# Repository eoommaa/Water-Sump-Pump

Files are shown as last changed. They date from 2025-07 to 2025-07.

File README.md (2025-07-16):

# Water Sump Pump Countdown Timer
A countdown timer for managing a water sump pump using a Raspberry Pi Pico programmed in MicroPython, designed for SLAC National Accelerator Laboratory during Summer 2024.
- **Features:** Automates sump pump intervals and relay activation with a 60-minute countdown timer, 3-button control (`START`/`STOP`/`RESET`), and thermal safety from 80°F fan activation to prevent overheating
  - Each button (`START`/`STOP`/`RESET`) is mapped to an LED and activates a specific state when the user presses on it
  - 60-minute countdown timer displayed in `MM:SS` format with the temperature on the LCD (`Countdown: 60:00` & `Temp: 80 F`)
  - **LCD Library from [`RPI-PICO-I2C-LCD`](https://github.com/T-622/RPI-PICO-I2C-LCD/tree/main) by [`T-622`](https://github.com/T-622):** [`lcd_api`](/src/lcd/lcd_api.py) & [`pico_i2c_lcd`](/src/lcd/pico_i2c_lcd.py)
- **Components:** [Full BOM](docs/BOM.md) with relay and sump pump specs

# Schematics[^1][^2]

## SLAC Water Sump Pump Countdown Timer Schematic


## RP2040 Water Sump Pump Countdown Timer Schematic


# Relay Behavior
Relay controls the 120 VAC outlet like a feedback loop.
- **[`SLAC Water Sump Pump Countdown Timer` Schematic](#slac-water-sump-pump-countdown-timer-schematic):** Pin 3 from `K1` relay has an input of 120 VAC L input (10 A) and Pin 4 is an input to the same 120 VAC output
- **`START`:** Relay NC[^3] &rarr; Sump pump activates
- **`STOP` & `RESET`:** Relay NO[^3] &rarr; Sump pump deactivates

# `START`/`STOP`/`RESET` Button Controls
## `START`/`STOP`/`RESET` Button State Diagram
```
               ┌──────────────────────────┐
               │                          ▼
┌────┐   ┌─────┴───┐   ┌────────┐   ┌─────────┐
│Idle├──►│START Btn├──►│STOP Btn├──►│RESET Btn│
└────┘   └─────────┘   └────┬───┘   └────┬────┘
              ▲             ▼            │
              └──────────────────────────┘
```

## `START` Button
- **Function:** Default state where the system starts 60-minute countdown timer
- **LED:** Blinking green

## `STOP` Button
- **Function:** Pauses the countdown timer
- **LED:** Solid red
- **LCD:** Displays messages repeatedly
  > Countdown stopped!
  
  > Press START or RESET
- [`countdown_stop = True`](https://github.com/eoommaa/Water-Sump-Pump/blob/d4ba52d33f075a21b61ff5ee6c35b372b952a699/src/water_sump_pump.py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) pauses the countdown timer

### `START` & [`RESET`](#reset-button) Button on `STOP`
- **`START`:** Countdown timer continues from the time it was paused on
  - **LED:** Red off and blinking green

## `RESET` Button
- **Function:** Emergency reset (Countdown timer restarts at `60:00` after the user presses `START` button)
- **LED & Buzzer** Blinking blue & buzzer beeps repeatedly
- **LCD:** Displays messages repeatedly
  > Countdown reset!
  
  > Press START to start over
- [`system_locked = True`](https://github.com/eoommaa/Water-Sump-Pump/blob/d4ba52d33f075a21b61ff5ee6c35b372b952a699/src/water_sump_pump.py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) allows the user one button to press on to restart the countdown timer
  - User can press on `STOP` or `RESET` button, but the program ignores the two button presses when in `RESET` mode

## Countdown Idle and Completion LCD Messages
- **Countdown Idle:** `Press START!`
- **Countdown Completion:** `Press START to start agn`

# Notes
- **[`SLAC Water Sump Pump Countdown Timer` Schematic](#slac-water-sump-pump-countdown-timer-schematic):** A `K1` relay is connected to the L298N motor driver, which is the component connected in the final hardware
- **[`RP2040 Water Sump Pump Countdown Timer` Schematic](#rp2040-water-sump-pump-countdown-timer-schematic):** A 5V DC motor is used since the relay acts like a switch along with an IC2 1602 LCD connected to the RP2040
  - Ex: Motor on when countdown timer is running and vice versa when it is off
- **Power Indicator:** Green LED stays on during both idle and after completion states to indicate that the Pi Pico is powered

# Credit
- **LCD Library:** Adapted from [`RPI-PICO-I2C-LCD`](https://github.com/T-622/RPI-PICO-I2C-LCD/tree/main) by [`T-622`](https://github.com/T-622)

[^1]: [`SLAC Water Sump Pump Countdown Timer` Schematic](https://github.com/eoommaa/Water-Sump-Pump/blob/main/kicad/schematics/SLAC%20Water%20Sump%20Pump.pdf) and [`.kicad_sch`](https://github.com/eoommaa/Water-Sump-Pump/blob/main/kicad/SLAC%20Water%20Sump%20Pump.kicad_sch)
[^2]: [`RP2040 Water Sump Pump Countdown Timer` Schematic](https://github.com/eoommaa/Water-Sump-Pump/blob/main/kicad/schematics/RP2040%20Water%20Sump%20Pump.pdf) and [`.kicad_sch`](https://github.com/eoommaa/Water-Sump-Pump/blob/main/kicad/RP2040%20Water%20Sump%20Pump.kicad_sch)
[^3]: Normally open (NO) & normally closed (NC)

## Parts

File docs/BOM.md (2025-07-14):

# Bill of Materials
*Note: Components used for prototyping*

| Hardware | Qty | Notes |
| :--: | :--: | :--: |
| Raspberry Pi Pico | 1 | RP2040 MCU |
| L298N Motor Driver | 1 | Fan & motor/relay control |
| 9V DC Battery | 1 | Power source for L298N motor driver |

| User Control | Qty | Notes |
| :--: | :--: | :--: |
| NO[^1] Buttons | 3 | `START`/`STOP`/`RESET` |

| User Feedback | Qty | Notes |
| :--: | :--: | :--: |
| LEDs | 3 | Green (`START`), Red (`STOP`), Blue (`RESET`) |
| I2C 1602 LCD | 1 | Displaying countdown time & temp |
| Piezoelectric Buzzer | 1 | Beeps on `RESET` button |

| System Feedback | Qty | Notes |
| :--: | :--: | :--: |
| 5V DC Fan | 1 | Thermal safety |
| 5V DC Motor | 1 | Relay testing |

| Passive Components | Qty | Notes |
| :--: | :--: | :--: |
| 330 &#8486; Resistors | 3 | LEDs current limiting |
| 100 &mu;F Capacitors | 3 | Button debouncing |

# Relay and Sump Pump Specs
*Note: Similar components connected in the final hardware*
| Components | Manufacturer Part Number | Datasheet | Notes |
| :--: | :--: | :--: | :--: |
| Relay | AZ9375-1A-24DEF | [AZ9375 SENSITIVE SUBMINIATURE RELAY](https://www.azettler.com/pdfs/az9375.pdf) | 12 VDC coil, 120 VAC (10 A) |
| Sump Pump | PF92342-PB | [PF92342 Thermoplastic Sump Pump](https://fergusonprod.a.bigcontent.io/v1/static/5097488_7397986_specification) | 2400 GPH at 0' lift |

[^1]: Normally open (NO)

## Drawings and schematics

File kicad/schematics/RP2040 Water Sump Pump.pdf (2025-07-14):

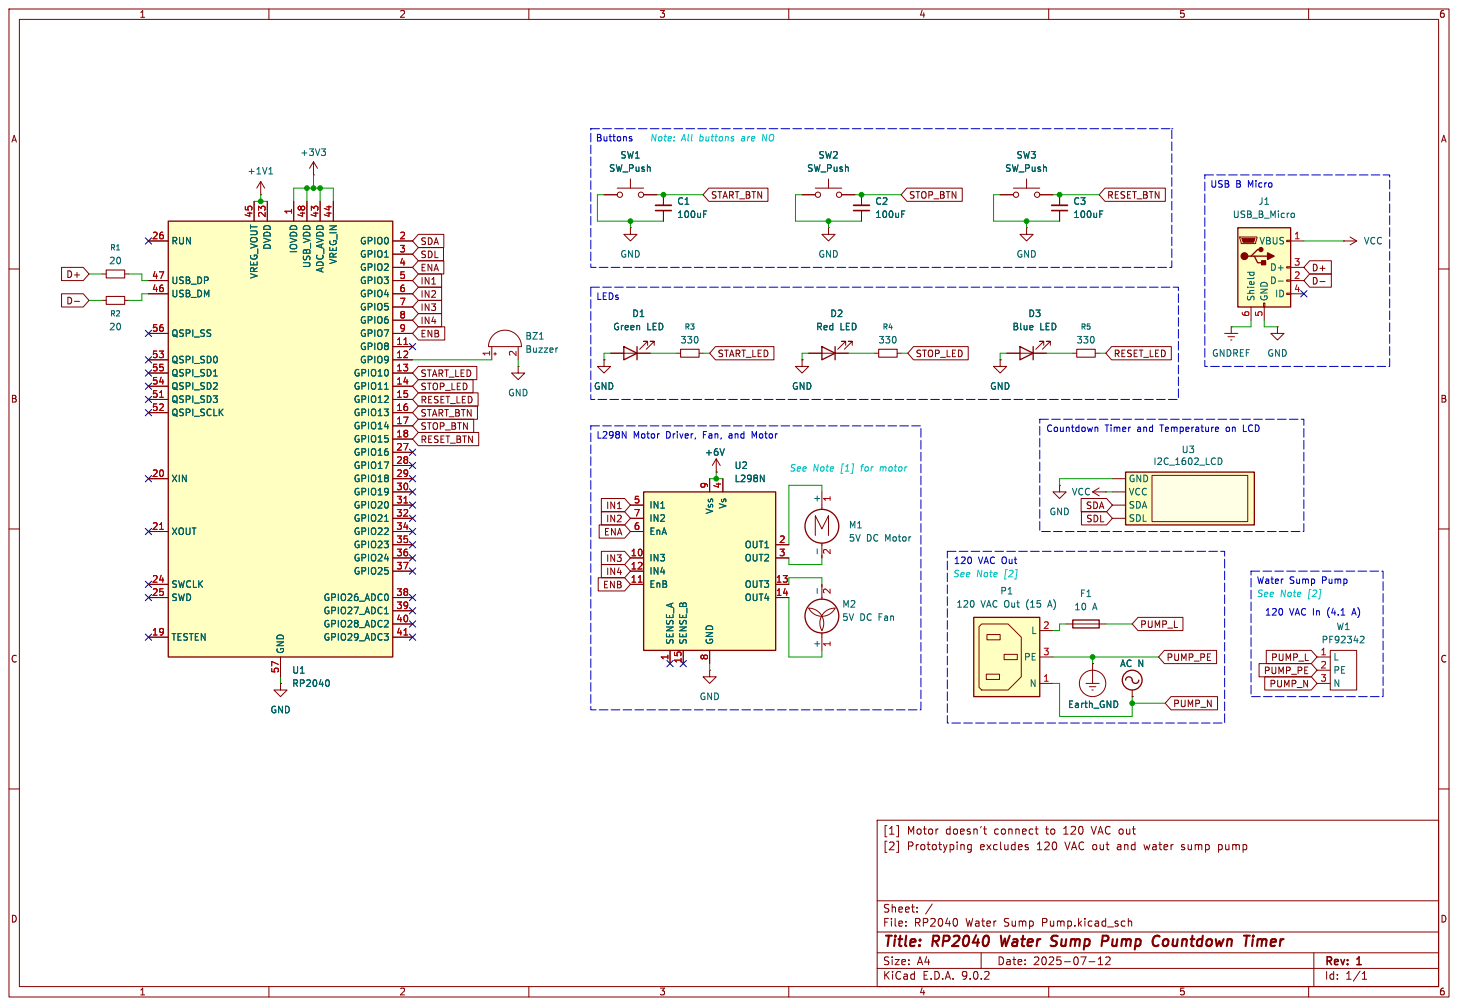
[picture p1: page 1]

L298N Motor Driver, Fan, and Motor C1

R4 330 D2 Red LED GND GND

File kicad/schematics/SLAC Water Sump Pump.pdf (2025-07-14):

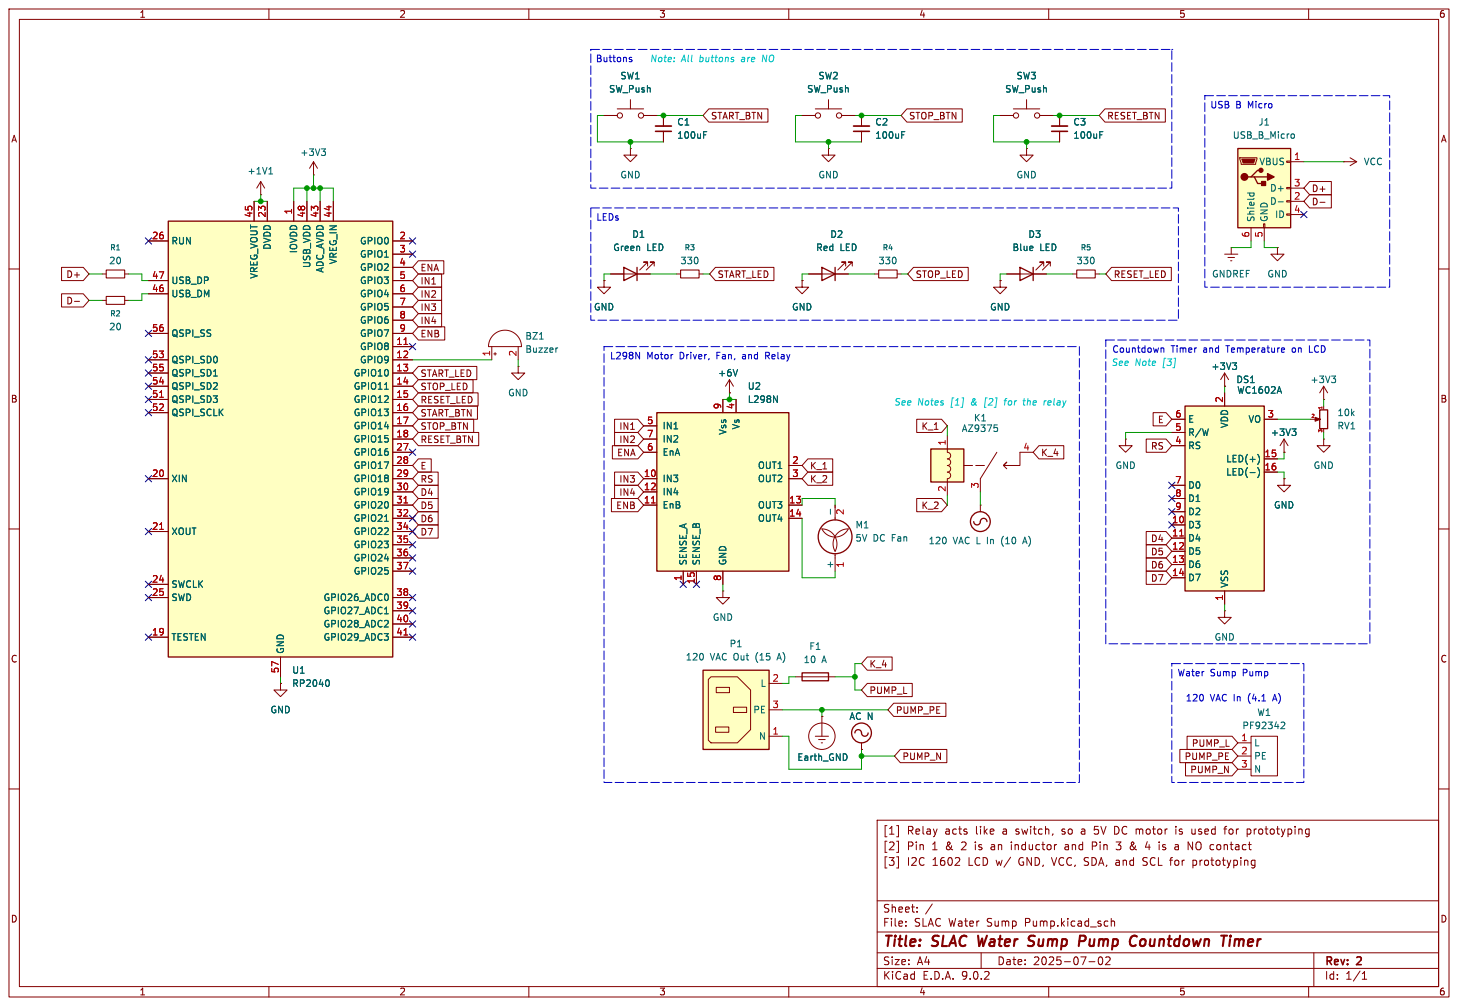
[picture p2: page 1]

Note: All buttons are NO

2 BZ1 Buzzer D2 Red LED GND GND

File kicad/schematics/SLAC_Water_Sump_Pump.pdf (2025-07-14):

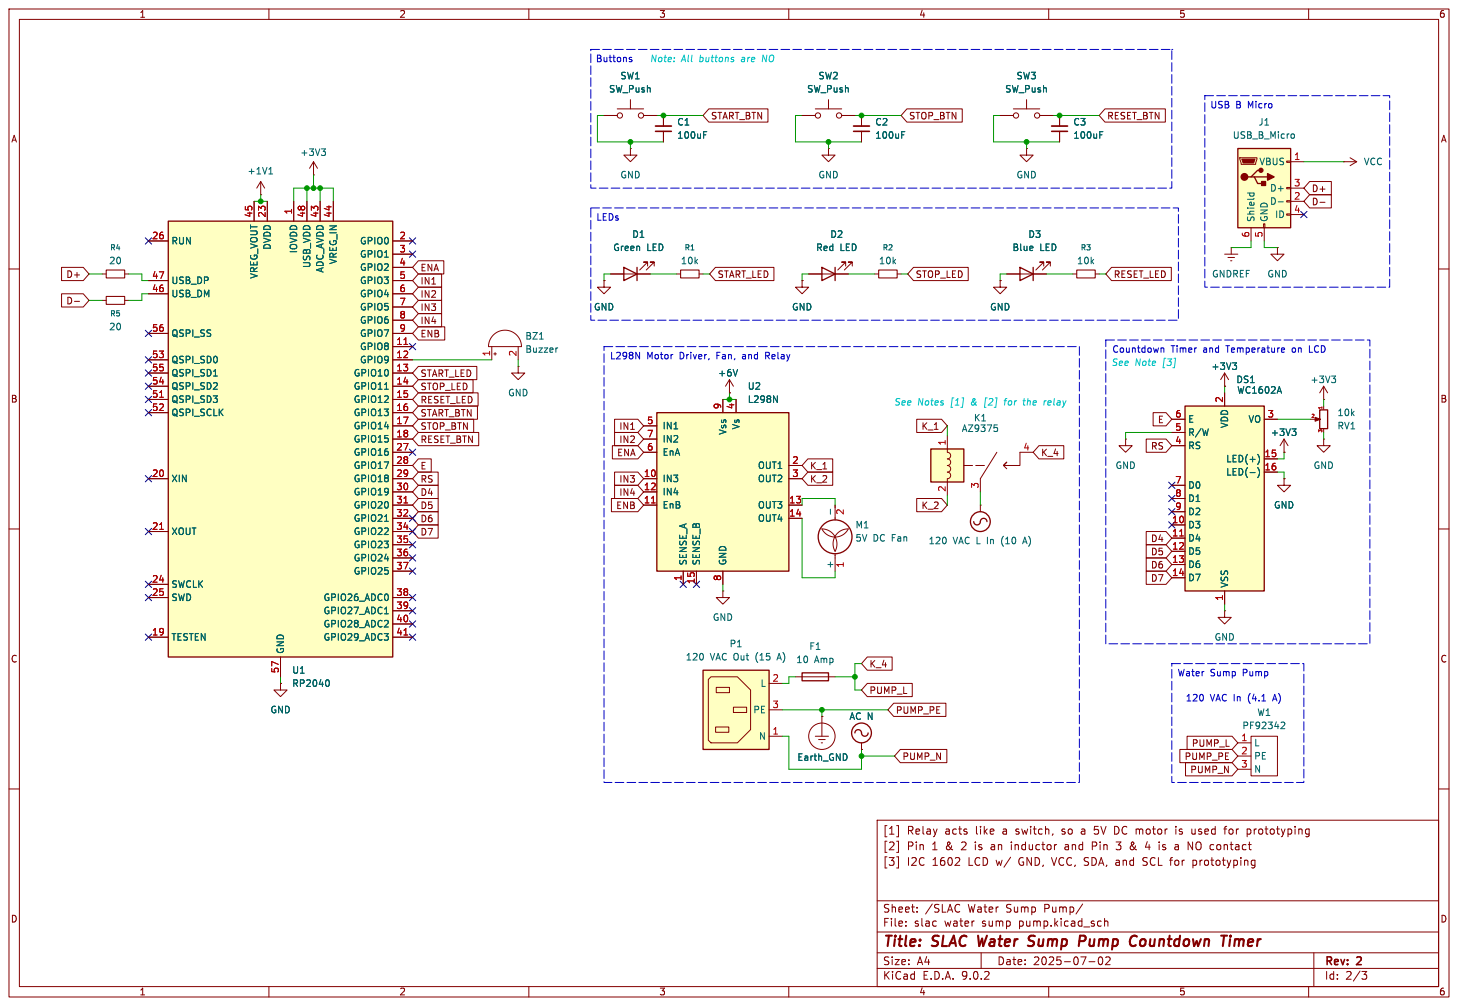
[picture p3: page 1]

2 BZ1 Buzzer GND GND GND

8 Vs 4 OUT1 2 OUT2 3 OUT3 13 OUT4 14 +6V U1 RP2040 RUN 26 USB_DP 47 USB_DM 46 QSPI_SS 56 QSPI_SD0 53 QSPI_SD1 55 QSPI_SD2 54 QSPI_SD3 51 QSPI_SCLK 52 XIN 20 XOUT 21 SWCLK 24 SWD 25 TESTEN 19 VREG_VOUT 45 DVDD 23 GND 57 IOVDD

120 VAC In (4.1 A) Water Sump Pump

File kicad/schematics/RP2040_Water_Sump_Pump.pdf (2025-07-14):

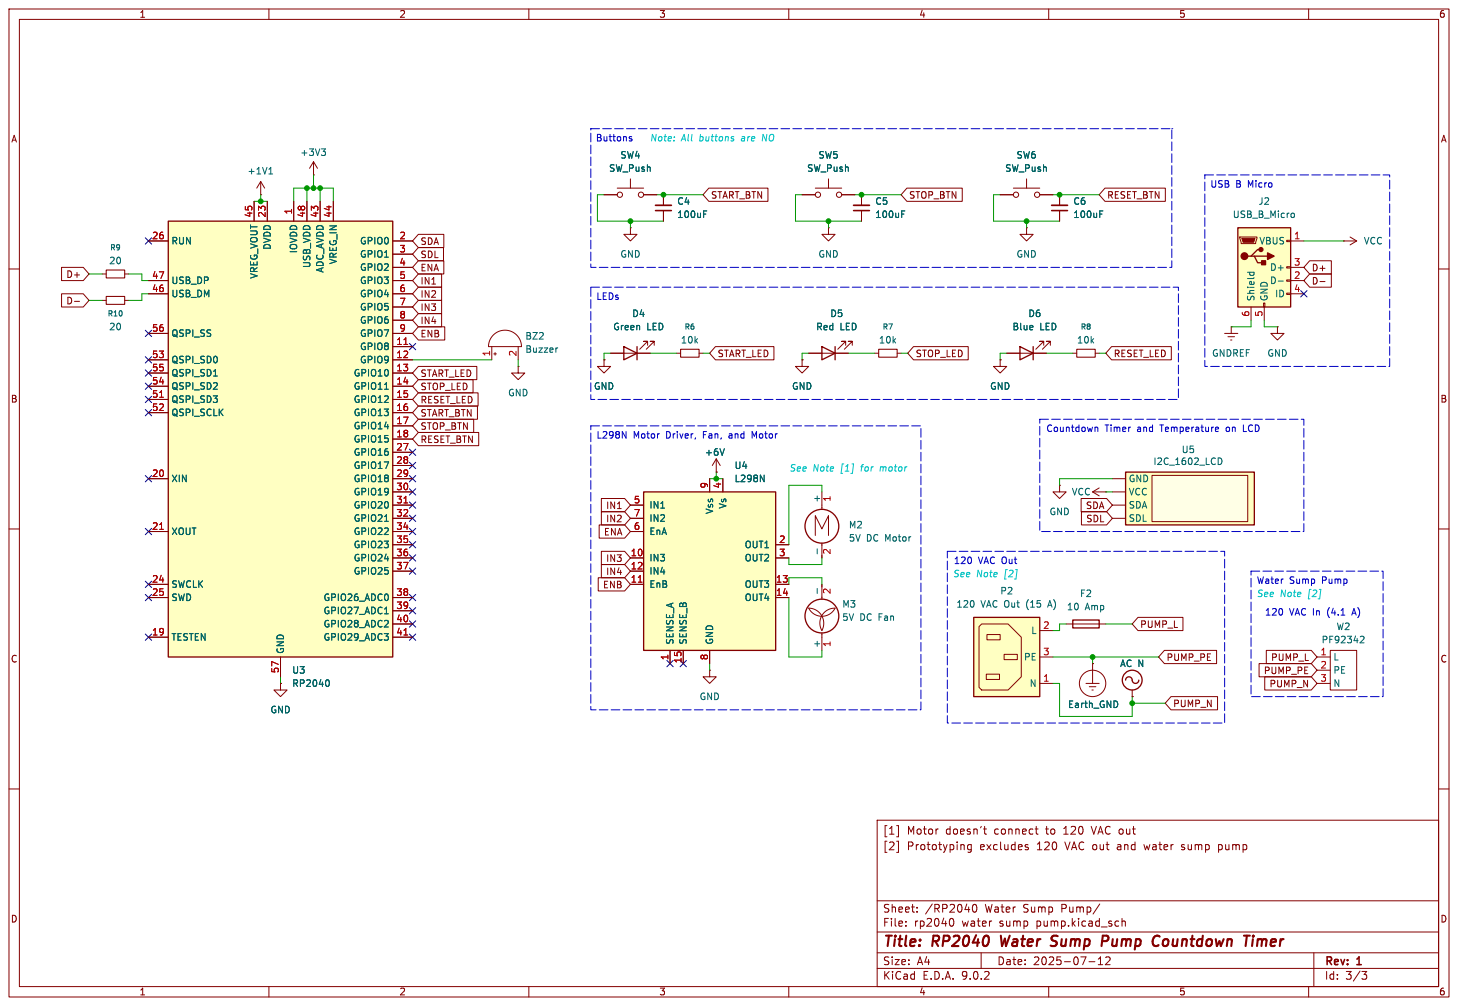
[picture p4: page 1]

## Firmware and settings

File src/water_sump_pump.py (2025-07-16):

'''
Water Sump Pump Countdown Timer V5

--- SETUP INSTRUCTIONS ---
READ BEFORE RUNNING THIS FILE
1. Save 3 Pico LCD files to the Pi Pico:
    - `lcd_api.py`
    - `pico_i2c_lcd.py`
    - `pico_i2c_lcd_test.py`
1a. Important: Do NOT rename the files. Keep original filenames
2. Run pico_i2c_lcd_test.py to verify LCD functionality
3. Optional: Rename this file to `main.py` if the Pi Pico will be connected to a power source (e.g., power bank) instead of the computer
4. Run this file on a MicroPython IDE (e.g., Thonny or PyCharm) when the Pi Pico is connected to the computer

--- VERSION HISTORY ---
V1&2: N/A
V3: Fixed STOP btn
V4: Added fan to L298N motor driver. Fan activation @ Temp >= 80°F
V5: Changed variable names, components' GPIO pins, and organized comments
'''

import time
from machine import Pin, I2C, Timer, ADC
from lcd_api import LcdApi
from pico_i2c_lcd import I2cLcd

I2C_ADDR = 0x27
I2C_NUM_ROWS = 2
I2C_NUM_COLS = 16

i2c = I2C(0, sda=Pin(0), scl=Pin(1), freq=400000)
lcd = I2cLcd(i2c, I2C_ADDR, I2C_NUM_ROWS, I2C_NUM_COLS)


# GPIO Pins for buzzer, LEDs (G, R, B), btns, and L298N motor driver
buzzer = Pin(9, Pin.OUT)
start_led = Pin(10, Pin.OUT)
stop_led = Pin(11, Pin.OUT)
reset_led = Pin(12, Pin.OUT)

start_btn = Pin(13, Pin.IN, Pin.PULL_UP)
stop_btn = Pin(14, Pin.IN, Pin.PULL_UP)
reset_btn = Pin(15, Pin.IN, Pin.PULL_UP) 

# L298N motor driver GPIO pins
ENA = Pin(2, Pin.OUT)		# Enable A. Motor/Relay
IN1 = Pin(3, Pin.OUT)
IN2 = Pin(4, Pin.OUT)
ENB = Pin(7, Pin.OUT)		# Enable B. Fan
IN3 = Pin(5, Pin.OUT)
IN4 = Pin(6, Pin.OUT)

# Initialize components on/off (1/0)
start_led.value(1)
stop_led.value(0)
reset_led.value(0)
buzzer.value(0)
IN1.value(0)
IN2.value(0)

# LCD at the beginning
lcd.clear()
lcd.putstr("Press START!")


'''
System State Flags
- Initialize system (sys), countdown timer (countdown in the code), and countdown time
- Sys and countdown timer set to false means the both are running normally
- system_locked: True → Sys locked via RESET btn
- countdown_stop: True → Pauses countdown via STOP btn
- initial_countdown_time: Time in sec (e.g., 3600s = 1 hr). Change to 5s for prototyping
'''
system_locked = False
countdown_stop = False
initial_countdown_time = 3600
countdown_time = initial_countdown_time

'''
Hardware Timers & Sensor
- start_led_timer: Blinking G LED during countdown
- buzzer_timer: Buzzer on during RESET (or system_locked)
'''
stop = 1
start_led_timer = Timer()
buzzer_timer = Timer()
temp_sensor = ADC(4)		# Internal temp sensor connected to ADC channel 4


# Functions for LEDs, buzzer, relay, fan, and temp
def blink_start_led(timer):
    start_led.toggle()
    
def blink_reset_led(timer):
    reset_led.toggle()
    
def beep_buzzer(timer):
    buzzer.toggle()

'''
Relay Prototyping
- Motor used as a relay
- Note: relay_NC/relay_NO can be rename to motor_on/motor_off
'''
def relay_NC():
    ENA.value(1)
    IN1.value(1)
    IN2.value(0)

def relay_NO():
    ENA.value(0)
    IN1.value(0)
    IN2.value(0)
    
def fan_on():
    ENB.value(1)
    IN3.value(1)
    IN4.value(0)
    
def fan_off():
    ENB.value(0)
    IN3.value(0)
    IN4.value(0)

def control_fan(temp_F):
    if temp_F >= 80:
        fan_on()
    else:
        fan_off()

'''
Internal Temp Reading in F
- temp_sensor.read_u16: Reads 16-bit ACD
- ADC_voltage: Converts 16-bit ACD to voltage
'''
def read_temp():
    ADC_voltage = temp_sensor.read_u16() * (3.3 / 65535)
    temp_C = 27 - (ADC_voltage - 0.706) / 0.001721
    temp_C = max(min(temp_C, 80), -20)
    temp_F = (1.8 * temp_C) + 32
    return round(temp_F, 1)


'''
Countdown Timer Function
- Motor/Relay control, LED indicator, temp monitoring
- Button handling (STOP & RESET)
    STOP: countdown_stop, solid R LED, relay NO
    RESET: system_locked, blinking B LED, relay NO, buzzer beep
- `return`: Exit countdown
    STOP: Sys enters paused state
    RESET: Sys is locked
'''
def countdown():
    # Initialize countdown
    global countdown_time, countdown_stop, stop
    countdown_stop = False		# Countdown starts
    relay_NC()
    start_led_timer.init(period=500, mode=Timer.PERIODIC, callback=blink_start_led)
    
    for i in range(countdown_time, 0, -1):		# (initial time in sec | final | inc/dec)
        countdown_time = i						# Update countdown time
        if start_btn.value() == 0:
            print("START btn pressed! → Relay NC")
        
        # STOP Btn Handling
        if stop_btn.value() == 0:
            countdown_stop = True
            stop = 0
            start_led.value(0)
            start_led_timer.deinit()	# `deinit` stops START (green) LED blinking
            stop_led.value(1)
            relay_NO()
            print("STOP btn pressed! → Relay NO")
            time.sleep(2)
            return
        
        # RESET Btn Handling
        if reset_btn.value() == 0:
            global system_locked
            system_locked = True
            relay_NO()    
            start_led_timer.deinit()
            start_led.value(0)
            buzzer_timer.init(period=500, mode=Timer.PERIODIC, callback=beep_buzzer)
            print("RESET btn pressed! → System locked, Relay NO, and Buzzer beep beep")
            return
        
        '''
        Countdown Timer on LCD
        - Convert seconds to MM:SS format
        - LCD Line 1: Countdown & Line 2: Temp
        '''
        temp = read_temp()		# Read temp
        min = i // 60
        sec = i % 60
        lcd.clear()
        lcd.putstr(f"Countdown: {min:02}:{sec:02}")
        lcd.move_to(0, 1)
        lcd.putstr(f"Temp: {temp} F")       
        print(f"Countdown: {min:02}:{sec:02} Temp: {temp}°F")
        time.sleep(1)
        
    '''
    Countdown Timer 00:00 Time
    - LCD displays 00:00 when countdown completes
    - START (green) LED always on after countdown is done
    - countdown_time: Reset countdown time to 60:00 when it reaches 00:00
    '''
    lcd.clear()
    lcd.putstr("Countdown: 00:00")
    lcd.move_to(0, 1)
    lcd.putstr(f"Temp: {temp:.2f} F")
    time.sleep(2)
    lcd.clear()
    lcd.putstr("Press START to")
    lcd.move_to(0, 1)
    lcd.putstr("start agn")
        
    start_led.value(1)
    countdown_time = initial_countdown_time
    start_led_timer.deinit()
    relay_NO()
    print(f"Countdown: 00:00 Temp: {temp:.2f}°F")
    print("Countdown done → Relay NO")

'''
Main Control Loop - Button Handling
- Continuous temp monitoring
    control_fan: Automatically based on temp
- STOP: START & RESET btns
- RESET: START btns
- LCD displays specific messages repeatedly when in STOP/RESET mode
'''
while True:
    temp = read_temp()
    control_fan(temp)
    
    # START Btn Handling
    if start_btn.value() == 0 and not system_locked:
        reset_led.value(0)
        stop_led.value(0)
        lcd.clear()
        lcd.move_to(0, 1)
        temp = read_temp()
        lcd.putstr(f"Temp: {temp:.2f} F")
        countdown()
    
    '''
    STOP Btn Options (2)
    1. START: Resume countdown from the time paused on
    2. RESET: Restart the countdown at 60:00 after pressing START btn
    `break`: Exit STOP mode when START/RESET btn pressed
    '''
    if stop == 0:
        while True:
            lcd.clear()
            lcd.putstr("Countdown")
            lcd.move_to(0, 1)
            lcd.putstr("stopped!")
            time.sleep(0.5)
            lcd.clear()
            lcd.putstr("Press START or")
            lcd.move_to(0, 1)
            lcd.putstr("RESET")
            time.sleep(0.5)
            
            if start_btn.value() == 0:
                stop_led.value(0)
                lcd.clear()
                lcd.putstr("START btn")
                lcd.move_to(0, 1)
                lcd.putstr("pressed")
                print("START btn pressed! → Relay NC")
                time.sleep(2)
                stop = 1
                countdown()
                break
            
            if reset_btn.value() == 0:
                stop_led.value(0)
                system_locked = True
                reset_led.value(1)
                buzzer_timer.init(period=500, mode=Timer.PERIODIC, callback=beep_buzzer)
                print("RESET btn pressed! → System locked, Relay NO, and Buzzer beep beep")
                lcd.clear()
                lcd.putstr("RESET btn")
                lcd.move_to(0, 1)
                lcd.putstr("pressed")
                stop = 1
                time.sleep(2)
                break
        
    '''
    RESET Btn Option (1)
    1. START: Restart countdown at 60:00
    '''
    if system_locked:
        start_led.value(0)
        reset_led.toggle()
        time.sleep(0.4)
        
        lcd.clear()
        lcd.putstr("Countdown reset!")
        time.sleep(0.4)
        lcd.clear()
        lcd.putstr("Press START to")
        lcd.move_to(0, 1)
        lcd.putstr("start over")
        time.sleep(0.5)
        
        if start_btn.value() == 0:
            system_locked = False
            buzzer_timer.deinit()
            buzzer.value(0)
            countdown_time = initial_countdown_time
            reset_led.value(0)
            lcd.clear()
            lcd.putstr("START btn")
            lcd.move_to(0, 1)
            lcd.putstr("pressed")
            time.sleep(2)
            
            lcd.clear()
            lcd.putstr("Restarting countdown soon...")
            print("START btn pressed! Restarting countdown!")
            time.sleep(2)
            countdown()   
        continue			# Sys locked skips STOP & RESET until START is pressed

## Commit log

2025-07-11 edit bom
2025-07-14 Rename RP2040 Water Sump Pump.pdf to RP2040_Water_Sump_Pump.pdf
2025-07-14 Rename SLAC Water Sump Pump.pdf to SLAC_Water_Sump_Pump.pdf
2025-07-14 Rename SLAC_Water_Sump_Pump.pdf to SLAC Water Sump Pump.pdf
2025-07-14 Rename RP2040_Water_Sump_Pump.pdf to RP2040 Water Sump Pump.pdf
